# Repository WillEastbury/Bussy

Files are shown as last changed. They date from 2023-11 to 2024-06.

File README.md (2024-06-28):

# Bussy McBusFace
## Smart Taps (Campervan Water System)

If you've ever used the pressure-switched type of water system in a campervan / RV, you'll know how much of a pain they are to calibrate and use. So I snapped one day and designed my own Smart Water System for my Campervan. 

---------------------------------

This repo includes the designs for a Raspberry Pi 4 based .net WebServer that can update an Grove LCD RGB based display(I2C) and read 2x Grove ultrasonic ranger sensors to sense the water level in the clean tank and grey waste tank, if mains water is not connected to the vehicle (Sensed via a gpio switch). 

I've also included the diagram to build and wire it, and the associated 3D printer file to print the button housing.

The Pi .net 6-based server receives data from 2x RaspberryPi Pico W devices that have attached buttons for hot and cold water (Connected to digital LED buttons on a Grove Pi Pico Shield).

These Pico W devices connect to the server .net minimal API to request hot or cold water on a button press.

There is a third connected PicoPi W device, attached into a Relay Box with 8 attached DC relays which respond to data polled from the buttons to energise the relays to enable the following 12V supply connectors :-

There is an LPG gas boiler connected through the Hot Water Boiler Enabled Solenoid to provide on-demand hot water. 
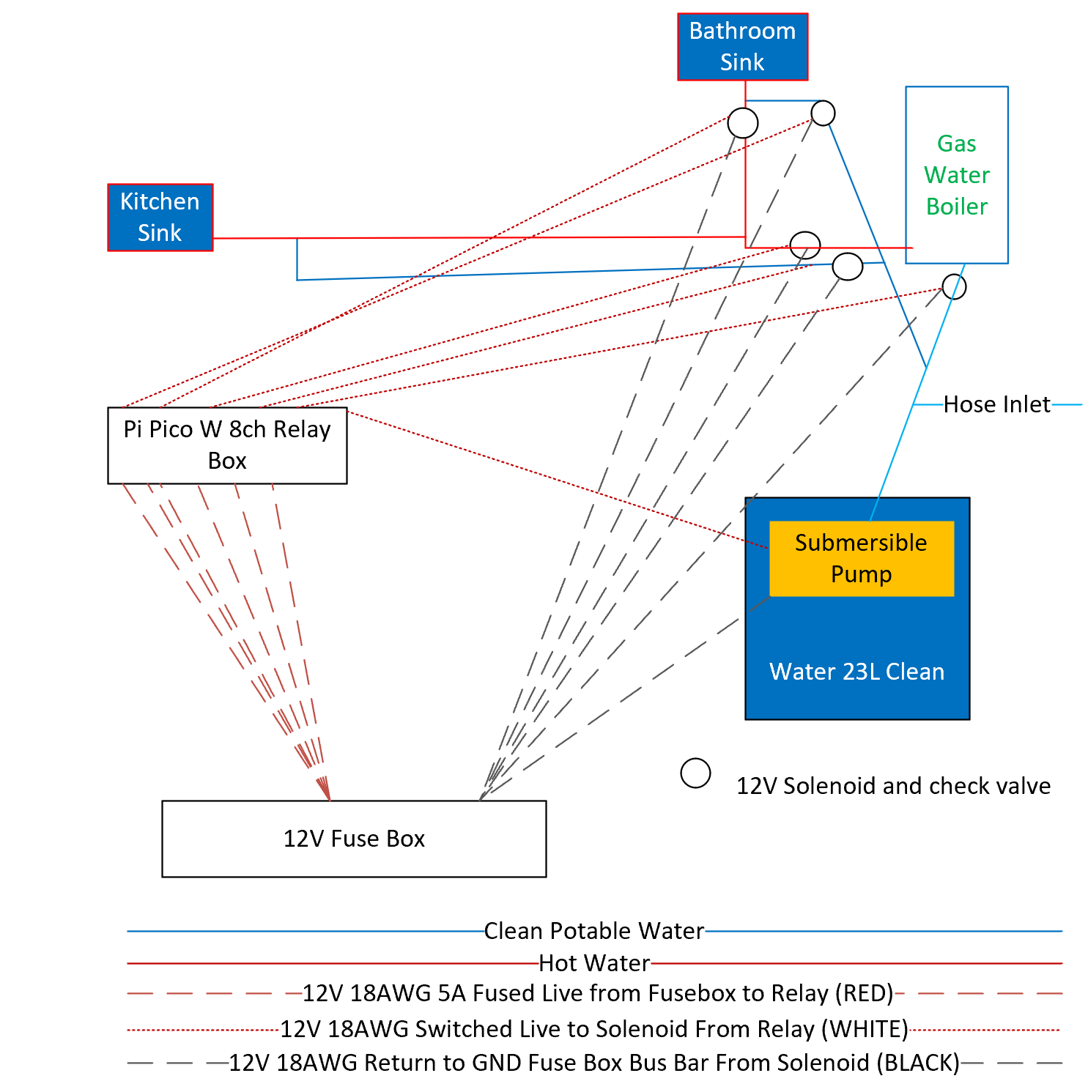
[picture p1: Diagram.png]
Connection Diagram


----------------------------------
Here it is assembled and on test before install into BussyMcBusFace :- 

Test Image On Test 

Web Image Testing Webserver 

In the repo, I provide Arduino Sketches for the picos, .net project source code for 2x .net Daemons (1x for the Webserver control panel, one for the Display Output on the Pi). 

To rig the entire system you will need the following parts.

### Plumbing
- 5x 15mm DN15 12V Water Solenoids with check valve - https://thepihut.com/products/12v-solenoid-valve-1-2
- 1x 12v Submersible Water Pump (I used a Whale pump) - https://www.eurocarparts.com/p/whale-standard-12v-submersible-electric-pump-white-10-litres-gp1002-560773980
- 2x Fiamma 23L Tanks (1 blue (fresh) and 1 grey (waste)) - https://www.halfords.com/camping/water-and-waste/fiamma-roll-tank-23l-fresh-483158.html
- 2x 15mm Pushfit elbows (JG Speedfit)
- 5x 15mm Pushfit Equal Tees (JG Speedfit)
- 1x 10mm to 15mm Pushfit reducing coupler (JG Speedfit) 
- 2x 3m Some 15mm pex barrier pipe (JG Speedfit)
- 1x 3m 15mm Chrome Pipe 
- 4x 15mm Compression fit Chrome elbows
- 2x 15mm Compression fit Shower check valve 
- 4x 15mm to 15mm flexible hose (Push fit)

### External Water Plumbing
- Lengths of drainage pipe (25 / 35 mm and elbows + 1x equal tee) for drains
- 1x Hose Pipe to tap fitting
- 1x 12mm Hose to 15mm push fit adapter
- 1x 12mm Jubilee Clip

### Power
- 1x Campervan 12v supply or external 12v battery
- 1x Kohree 12 way 12V Fuse Box - https://www.amazon.co.uk/dp/B082KLBGGZ?psc=1&ref=ppx_yo2ov_dt_b_product_details
- 3x JZK 12V to Dual USB PSU - https://www.amazon.co.uk/dp/B06XSCCLCD?psc=1&ref=ppx_yo2ov_dt_b_product_details
- 1x box 18AWG hook up wire 
  
## Gas [Warning - get a GasSafe registered installer if you intend on a permanent install]
- 1x A gas boiler (10L CO-Z is the one I used), professionally installed and connected to an LPG tank
  - https://www.amazon.co.uk/CO-Z-Stainless-Liquefied-Petroleum-Certified/dp/B08YR3SXWY?th=1
- Or a simple gas bottle (Calor or CampingGaz) if you intend to put the boiler outside with a regulator and hose

### Compute
- 1x Raspberry Pi 4B (with Raspbian Linux installed, Wireless connected, and I2C enabled) - https://www.raspberrypi.com/products/raspberry-pi-4-model-b/
- 3x Raspberry Pi Pico WH (And the Arduino IDE installed and configured for Pi Pico W on your PC) - https://www.adafruit.com/product/5544
- 1x Small Breadboard
- Some small jumper wires for breadboard
- 2x Grove Jumper Female converters https://thepihut.com/products/grove-4-pin-female-jumper-to-grove-4-pin-conversion-cables-5-pack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
  
### Sensors and Actuators
- 1x GrovePi+ Shield (Optional, if you don't have one of these then you can wire up the I2C direct to the pins) - https://www.unmannedtechshop.co.uk/product/grovepi/
- 3x Grove Pico Shield - https://thepihut.com/products/grove-shield-for-raspberry-pi-pico-v1-0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
- 2x Grove Ultrasonic Ranger Sensor - https://thepihut.com/products/dexter-grovepi-and-gopigo-ultrasonic-sensor
- 2x Grove LED Button - Red - https://uk.rs-online.com/web/p/hmi-development-tools/1887114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,+Power+%26+Connectors-_-1887114&matchtype=e&pla-4574724306713135&cq_src=google_ads&cq_cmp=554644865&cq_term=&cq_plac=&cq_net=o&cq_plt=gp&gclid=482ae6ac33451e2dde7c83fb93661a1b&gclsrc=3p.ds&msclkid=482ae6ac33451e2dde7c83fb93661a1b
- 2x Grove 10 Segment LED Display 
- 2x Grove LED Button - Blue
- 2x Grove 0.96" OLED Yellow and Blue Display (SSD1315) - https://thepihut.com/products/grove-0-96-oled-yellow-blue-display-ssd1315
- 1x Grove LCD Backlight Display - https://uk.farnell.com/seeed-studio/104030001/grove-lcd-rgb-backlight-display/dp/3932101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
- 1x Grove Switch (P) - https://wiki.seeedstudio.com/Grove-Switch-P/
- 1x Waveshare Pico Relay B - https://www.waveshare.com/wiki/Pico-Relay-B

### Pinouts 
For convenience i've listed the pins and ports used below

DEFAULT SERVER ADDRESS http://192.168.200.36:5000

#### PINS RELAY CONTROLLER
const int SolenoidColdKitchenPin = 17;   // Channel 5
const int SolenoidHotKitchenPin = 16;    // Channel 6
const int SolenoidColdBathroomPin = 19;  // Channel 3
const int SolenoidHotBathroomPin = 18;   // Channel 4 
const int SolenoidBoilerControlPin = 20; // Channel 2
const int PumpColdPin = 21;              // Channel 1
const int LEDPin = 13;                   // RGB LED
const int BuzzerPin = 6;                 // Buzzer

#### PINS KITCHEN AND BATHROOM TAP CONTROLLERS

const int ColdButtonPin = 19;      // Cold Button = GPIO 16 on Pico (Grove D16)
const int ColdLEDPin = 18;         // Cold Button = GPIO 17 on Pico (Grove D16)
const int MainsWaterSelect = 16;    // Mains cold water and drainage in place
const int HotButtonPin = 21;       // Hot Button = GPIO 20 on Pico (Grove D20)
const int HotLEDPin = 20;          // Hot Button = GPIO 21 on Pico (Grove D20)

#### PINS CABINET SENSOR CONTROLLER 

int LEDPin = 12;
int LEDOnboard = 25;
Ultrasonic ultrasonicFresh(7);     // Yellow to Blue Fresh Tank
Ultrasonic ultrasonicDirty(9);     // Yellow to Grey Waste Tank
Grove_LED_Bar barFresh(4, 5, 0);   // white, yellow
Grove_LED_Bar barGrey(10, 11, 1);  // white, yellow

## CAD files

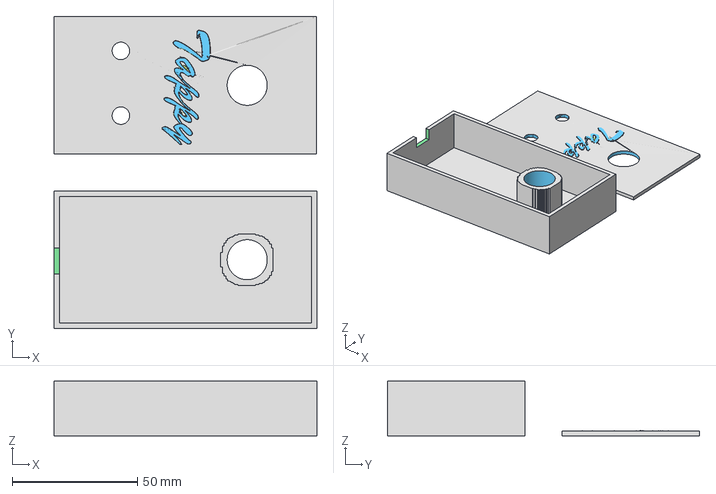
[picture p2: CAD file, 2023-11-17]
Tappy Mc Tap Face.3mf
105.0 x 124.7 x 21.9 mm

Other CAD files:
Tappy Mc Tap Face.stl

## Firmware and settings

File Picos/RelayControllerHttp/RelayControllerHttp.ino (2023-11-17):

#include <WiFi.h>
#include <HTTPClient.h>
#include <Arduino_JSON.h>
#include <string>


const char* ssid = "<InsertSSID>";
const char* password = "<InsertWPSPassword>";
String hostName = "RR_Cabinet      ";
String AuthKey = "<Insert_32_char_Shared_Key_Here>";
String serverAddress = "http://192.168.200.36:5000/";  // Replace with your server address

const int SolenoidColdKitchenPin = 17;   // Channel 5
const int SolenoidHotKitchenPin = 16;    // Channel 6
const int SolenoidColdBathroomPin = 19;  // Channel 3
const int SolenoidHotBathroomPin = 18;   // Channel 4 
const int SolenoidBoilerControlPin = 20; // Channel 2
const int PumpColdPin = 21;              // Channel 1
const int LEDPin = 13;                   // RGB LED
const int BuzzerPin = 6;                 // Buzzer

WiFiClient client;

void setup() {
  
  int LEDPinOnboard = 32; 
  pinMode(LEDPinOnboard, OUTPUT);
  digitalWrite(LEDPinOnboard, HIGH);

  Serial.begin(115200);
  WiFi.begin(ssid, password);

  while (WiFi.status() != WL_CONNECTED) 
  {
    delay(1000);
    Serial.println("Connecting to Wi-Fi...");
  }

  Serial.println("Wi-Fi connected successfully: " + WiFi.localIP().toString());
  pinMode(SolenoidColdKitchenPin, OUTPUT);
  pinMode(SolenoidHotKitchenPin, OUTPUT);
  pinMode(SolenoidColdBathroomPin, OUTPUT);
  pinMode(SolenoidHotBathroomPin, OUTPUT);
  pinMode(PumpColdPin, OUTPUT);
  pinMode(SolenoidBoilerControlPin, OUTPUT);
  pinMode(LEDPin, OUTPUT);
  pinMode(BuzzerPin, OUTPUT);
}

void loop() {
    fetchRelayStatus();
    delay(350);
}

void fetchRelayStatus() {
  HTTPClient http;
  String url = serverAddress + "api/calculations";  // Convert hostName to arduino::String
  String authHeader = hostName + AuthKey;
  // Serial.print("Connecting to url:");
  // Serial.println(url);
  // Perform HTTP request
  http.begin(url);
  //Serial.println(authHeader);
  http.addHeader("ServiceKey", authHeader);
  int httpResponseCode = http.GET();
  if (httpResponseCode == 200) 
  {
    digitalWrite(LEDPin, HIGH);
    JSONVar myObject = JSON.parse(http.getString());
    //Serial.print("HTTP Success! code: ");
    //Serial.println(httpResponseCode);
    //Serial.println(myObject);
    http.end();
    bool ICTIKO = myObject["IsColdTapInKitchenOn"];
    bool IHTIKO = myObject["IsHotTapInKitchenOn"]; 
    bool ICTIBO = myObject["IsColdTapInBathroomOn"];
    bool IHTIBO = myObject["IsHotTapInBathroomOn"]; 
    bool BSE = myObject["BoilerSolenoidEnabled"]; 
    bool PUMP = myObject["WaterPumpEnabled"]; 
    bool SHUTDOWN = myObject["WaterShutOff"]; 

    Serial.println("Got HTTP Data from Server");
    Serial.print("Kitchen Cold");Serial.println(ICTIKO);
    Serial.print("Kitchen Hot");Serial.println(IHTIKO);
    Serial.print("Bathroom Cold");Serial.println(ICTIBO);
    Serial.print("Bathroom Hot");Serial.println(IHTIBO);
    Serial.print("Boiler");Serial.println(BSE);
    Serial.print("Pump");Serial.println(PUMP); 
    Serial.print("SHUTDOWN");Serial.println(SHUTDOWN);

    digitalWrite(SolenoidColdKitchenPin, ICTIKO == true ? HIGH : LOW);
    digitalWrite(SolenoidHotKitchenPin, IHTIKO == true ? HIGH : LOW);
    digitalWrite(SolenoidColdBathroomPin, ICTIBO == true ? HIGH : LOW);
    digitalWrite(SolenoidHotBathroomPin,  IHTIBO == true ? HIGH : LOW);
    digitalWrite(SolenoidBoilerControlPin, BSE == true ? HIGH : LOW);
    digitalWrite(PumpColdPin, PUMP == true ? HIGH : LOW);
    digitalWrite(BuzzerPin, SHUTDOWN && PUMP == true ? HIGH : LOW);
  } 
  else 
  {
    // FailSafe
    digitalWrite(LEDPin, LOW);
    digitalWrite(SolenoidColdKitchenPin, LOW);
    digitalWrite(SolenoidHotKitchenPin, LOW);
    digitalWrite(SolenoidColdBathroomPin, LOW);
    digitalWrite(SolenoidHotBathroomPin, LOW);
    digitalWrite(SolenoidBoilerControlPin, LOW);
    digitalWrite(PumpColdPin, LOW);
    digitalWrite(BuzzerPin, LOW);
    Serial.print("HTTP error code: ");
    Serial.println(httpResponseCode);
    http.end();
  }
}

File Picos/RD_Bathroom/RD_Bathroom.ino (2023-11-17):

#include <WiFi.h>
#include <HTTPClient.h>
#include <Arduino_JSON.h>
#include <Arduino.h>
#include <string>
#include <Adafruit_GFX.h>
#include <Adafruit_SSD1306.h>

#define SCREEN_WIDTH 128
#define SCREEN_HEIGHT 64

Adafruit_SSD1306 display(SCREEN_WIDTH, SCREEN_HEIGHT, &Wire);

const char* ssid = "<InsertSSID>";
const char* password = "<InsertWPSPassword>";

String hostName = "Bathroom        ";
String AuthKey = "<Insert_32_char_Shared_Key_Here>";
String serverAddress = "http://192.168.200.36:5000/";  // Replace with your server address

const int ColdButtonPin = 19;      // Cold Button = GPIO 16 on Pico (Grove D16)
const int ColdLEDPin = 18;         // Cold Button = GPIO 17 on Pico (Grove D16)
const int MainsWaterSelect = 16;   // Mains cold water and drainage in place
const int HotButtonPin = 21;       // Hot Button = GPIO 20 on Pico (Grove D20)
const int HotLEDPin = 20;          // Hot Button = GPIO 21 on Pico (Grove D20)

WiFiClient client;
HTTPClient http;
String authHeader;
String hostshort;

void setup(void) {

  int LEDPinOnboard = 32; 
  pinMode(LEDPinOnboard, OUTPUT);
  digitalWrite(LEDPinOnboard, HIGH);


  Wire.setSDA(8);
  Wire.setSCL(9);
  Wire.begin();
 
  if(!display.begin(SSD1306_SWITCHCAPVCC, 0x3C)) {
    Serial.println(F("SSD1306 allocation failed"));
    for(;;);
  }

  authHeader = hostName + AuthKey;
  hostshort = hostName; 
  hostshort.trim();
  Serial.println(authHeader);
  Serial.begin(115200);
  WiFi.begin(ssid, password);
  while (WiFi.status() != WL_CONNECTED) 
  {
    delay(1000);
    Serial.println("Init >> Connecting to Wi-Fi...");
  }
  Serial.println("Init >> Wi-Fi connected successfully: " + WiFi.localIP().toString());
  pinMode(ColdButtonPin, INPUT);
  pinMode(HotButtonPin, INPUT);  
  pinMode(MainsWaterSelect, INPUT);  
  pinMode(ColdLEDPin, OUTPUT);
  pinMode(HotLEDPin, OUTPUT);  

}
void loop(void) {

  display.println("Hello, I'm Tappy Mc Tap Face!");
  delay(500);  

  JsonSendSensorData("C_" + hostshort, ! digitalRead(ColdButtonPin));
  JsonSendSensorData("H_" + hostshort, ! digitalRead(HotButtonPin));

  if (hostshort == "Bathroom") // Only the bathroom has the master override mains water connection switch :) 
  {
    JsonSendSensorData("MainsConnectedWater", digitalRead(MainsWaterSelect));
  }
  fetchRelayStatus();
  delay(250);
}

void JsonSendSensorData(String Sensor, bool value)
{
    std::string valueStr = std::to_string(value);
    String arduinoValueStr = String(valueStr.c_str());
    String rawUrl = serverAddress + "api/sensors/" + Sensor + "/" + arduinoValueStr;
    http.begin(rawUrl);
    http.addHeader("ServiceKey", authHeader);
    if (http.GET() == 200) 
    {
      Serial.print("HTTP Success -- Send: ");
    }
    else 
    {
      Serial.print("HTTP error -- Send: ");
    }
    Serial.print(Sensor);
    Serial.print(" | ");
    Serial.println(arduinoValueStr);
    http.end();
}
void fetchRelayStatus() {
 
  HTTPClient http;
  String url = serverAddress + "api/calculations";  // Convert hostName to arduino::String
  String authHeader = hostName + AuthKey;
  Serial.print("Connecting to url:");
  Serial.println(url);
  // Perform HTTP request
  http.begin(url);
  Serial.println(authHeader);
  http.addHeader("ServiceKey", authHeader);
  int httpResponseCode = http.GET();
  if (httpResponseCode == 200) 
  {
    JSONVar myObject = JSON.parse(http.getString());
    Serial.print("HTTP Success! code: ");
    Serial.println(httpResponseCode);
    Serial.println(myObject);
    http.end();

    
    bool ColdLEDState = LOW;
    bool HotLEDState = LOW;
    if (myObject["IsColdTapIn" + hostshort + "On"])
    {
      ColdLEDState = HIGH;
    }
    if (myObject["IsHotTapIn" + hostshort + "On"])
    {
      HotLEDState = HIGH;
    }
    digitalWrite(ColdLEDPin, ColdLEDState);
    digitalWrite(HotLEDPin, HotLEDState);

    display.clearDisplay();
    display.setTextSize(1);
    display.setTextColor(SSD1306_WHITE);
    display.setCursor(0,0);
    String place = hostshort + " Tappy:";
    
    String cold = myObject["IsColdTapIn" + hostshort + "On"] ? "ON" : "Off";
    //String colds = myObject["TimeHotTapIn" + hostshort + "On"];
    String hot = myObject["IsHotTapIn" + hostshort + "On"] ? "ON" : "Off";
    //String hots = myObject["TimeHotTapIn" + hostshort + "On"];
    String waste = myObject["WasteTankFull"] ? "YES" : "No";
    String clean = myObject["CleanTankEmpty"] ? "YES" : "No";
    String mains = myObject["OnMainsWater"] ? "Yes" : "NO";
    display.println(place);
    display.println("Connected to Bussy");
    display.print("Cold Tap: "); display.println(cold); //display.println(colds);
    display.print("Hot Tap: "); display.println(hot); //display.println(hots);
    display.print("Waste Full: "); display.println(waste); 
    display.print("Clean Empty: "); display.println(clean);
    display.print("On Mains Water: "); display.println(mains);
    display.display();
  } 
  else 
  {
    Serial.print("HTTP error code: ");
    Serial.println(httpResponseCode);
    http.end();
    display.clearDisplay();
    display.setTextSize(1);
    display.setTextColor(SSD1306_WHITE);
    display.setCursor(0,0);
    String place = hostshort + " Tappy:";
    
    display.println(place);
    display.println("Disconnected from Bussy");
    
    display.display();
  }
}
